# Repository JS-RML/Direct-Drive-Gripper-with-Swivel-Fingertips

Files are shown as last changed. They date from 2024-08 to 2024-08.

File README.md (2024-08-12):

# Direct-Drive Gripper with Swivel Fingertips (2024)

<!-- $\color{red}{\textsf{TOO MANY TYPOS! EACH TYPO IS A DEFECT!}}$ -->

We here introduce our latest direct-drive gripper. Compared to [the previous version](https://github.com/JS-RML/ddh_hardware) that we presented in [ICRA 2023](https://ieeexplore.ieee.org/document/10160263), the current one adopts swivel fingertips with passive compliance for enhanced adaptiveness. Follow the instructions below to create one. 

<p align = "center">

</p>

**Related repos**
- [**High-Speed Scooping (2024)**](https://github.com/JS-RML/Advanced-high-speed-scooping/tree/main)
- [**High-Speed Scooping (2022)**](https://github.com/JS-RML/high_speed_scooping)
- [**Direct-Drive Gripper (2022)**](https://github.com/JS-RML/ddh_hardware)

-----

# Table of Contents

- [Parts](#parts)
  - [Bill of Materials (BOM)](#bom)
    - [Off-the-Shelf Parts](#purchase)
    - [3D Printing](#3d-printing)
- [Motors](#motors)
  - [Motor Subassembly](#assemble-actuators)
  - [Wiring](#wiring)
    - [Power Supply](#power-supply)
    - [Encoder Connection](#encoder-connection)
    - [Motor Connection](#Motor-connection)
  - [Motor Calibration](#actuator-calibration)
    - [Calibrate ODrives](#calibrate-odrives)
    - [Calibrate Zero Position](#calibrate-zero-position)
- [Gripper](#Gripper)
  - [Finger Assembly ⨉2](#finger)
  - [Gripper Assembly](#gripper-assembly)
  - [Mounting](#mounting-ur10)
- [Customization](#customization)
  - [Mounting](#custom-mounting)
- [Getting Started](#getting-started)
  
-----

# Parts
Prepare for the following parts.

## Bill of materials (BOM)

### Off-the-shelf parts
- [T-motor gb54-2](https://store.tmotor.com/goods-445-GB54-2.html) X 4
- [Odrive s1](https://odriverobotics.com/shop/odrive-s1) X 4
- [AS5048A Encoder + solid magnet](https://ko.aliexpress.com/item/1005004239532357.html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) X 4
- [Bearing - outer-diameter = 100mm, inner-diameter = 6mm](https://kr.misumi-ec.com/vona2/detail/221000058378/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) X 12
- [Spring - spring constant = 2.0N/mm, length = 10mm, outer-diameter = 4φ](https://kr.misumi-ec.com/vona2/detail/110310295289/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) X 2
- [Wire terminal box](https://mini.freeship.co.kr/goods/content.asp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) X 1
- [Shielded cable](https://smartstore.naver.com/bantolmarket/products/10633794496) X 1
- [3-phase cable](https://smartstore.naver.com/shipdiy/products/7890381050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) X 3

### 3D Printing
- [Bearing_insert_holder](stl/bearing_insert_holder.stl) X 2
- [Bearing pin](stl/bearing_pin.stl) X 2
- [Distal link](stl/distal_link.stl) X 2
- [Distal tip cap left](stl/L_distal_tip_cap.stl) X 1
- [Distal tip spring version left](stl/L_distal_tip_spring_ver.stl) X 1
- [Distal tip cap right](stl/R_distal_tip_cap.stl) X 1
- [Distal tip spring version right](stl/R_distal_tip_spring_ver.stl) X 1
- [Finger tip](stl/finger_tip.stl) X 2
- [Motor shell](stl/motor_shell.stl) X 1
- [Motor plate](stl/motorplate.stl) X 4
- [Proximal link](stl/proximal_link.stl) X 2
- [Porximal link cap](stl/proximal_link_cap.stl) X 2
- [Proximal link pillar](stl/proximal_link_pillar.stl) X 2
- [Rotation limiter](stl/rotation_limiter.stl) X 2

# Motors
Parts related to motors can be put together as follows.
$\color{red}{\textsf{Missing links to the images below.}}$

## Motor Subassembly
We need four motor subassemblies. Each one can be assembled as follows.
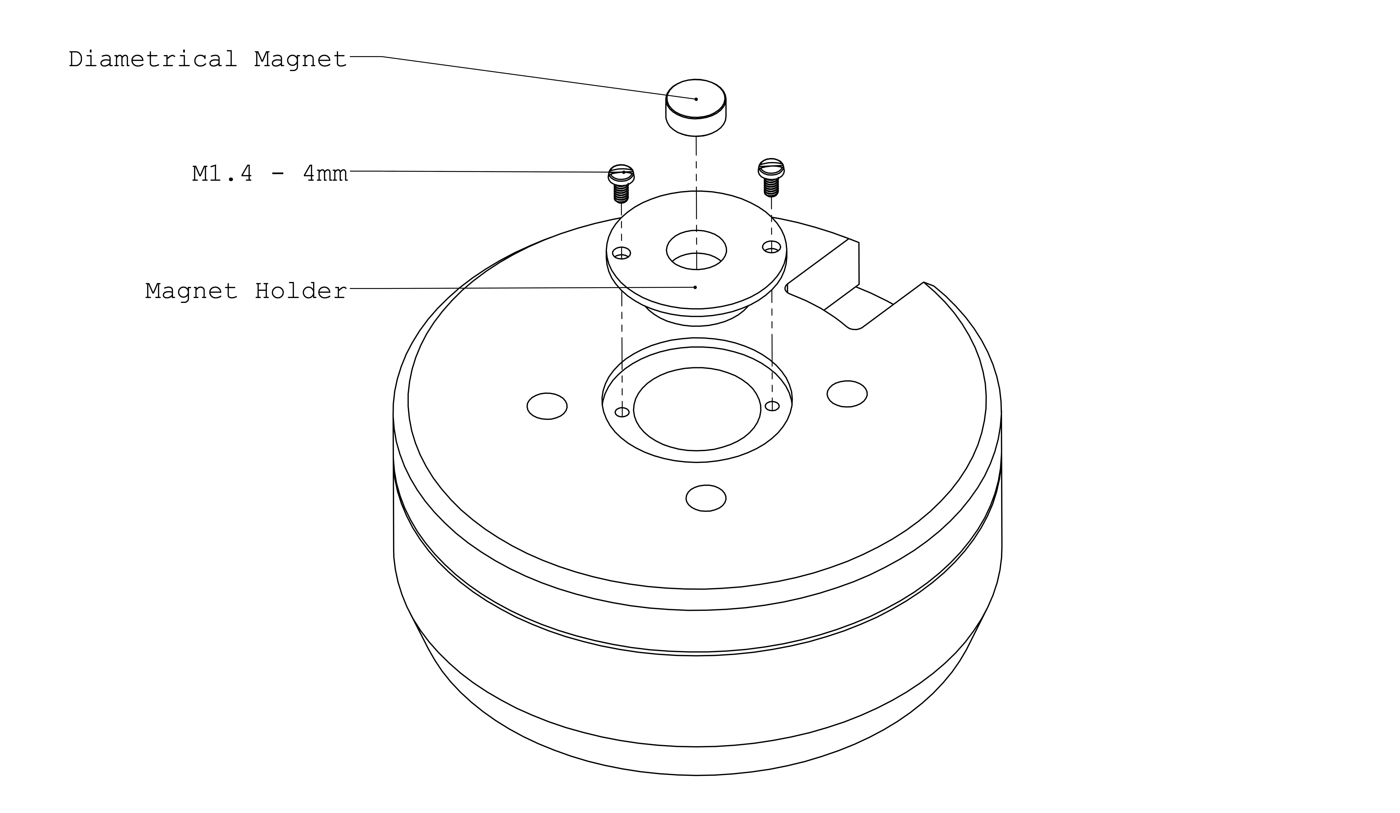
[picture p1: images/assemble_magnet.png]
motor_with_magnet

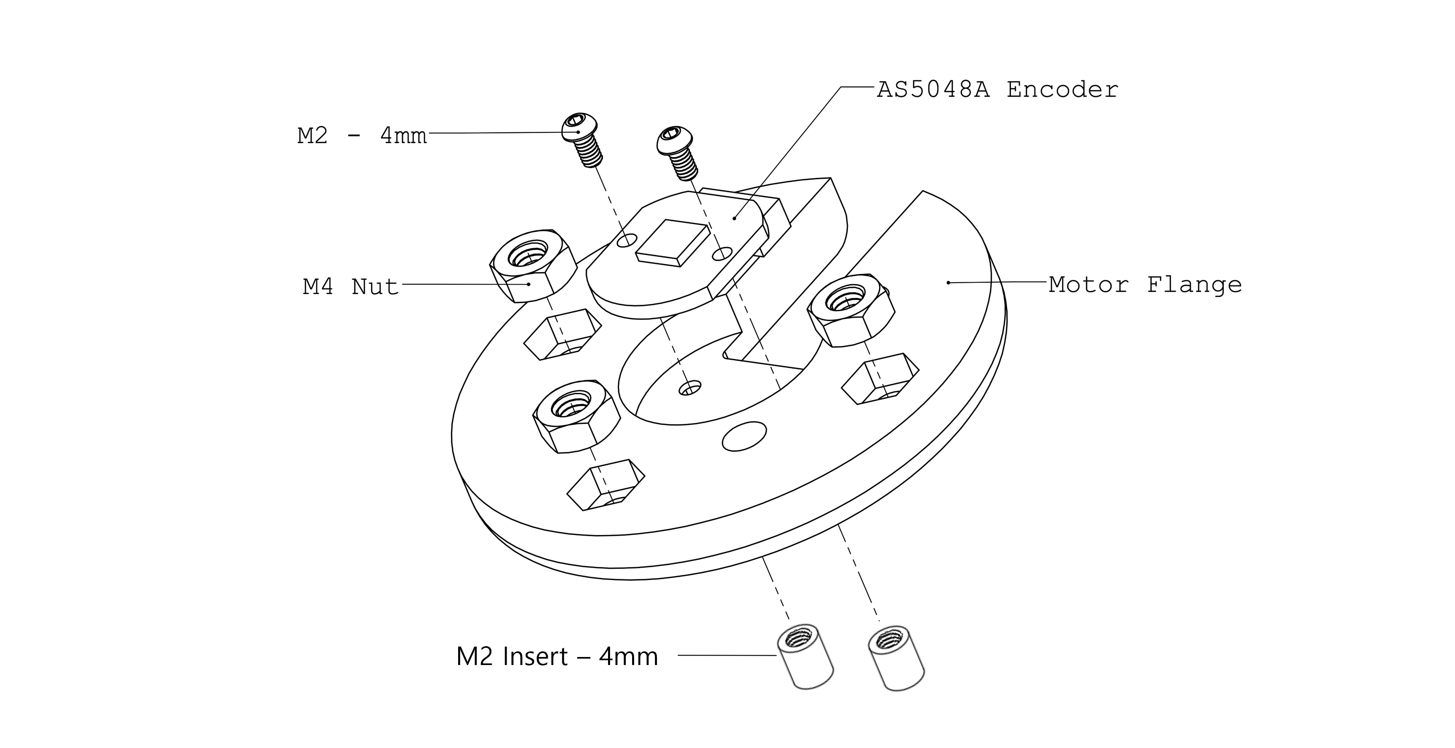
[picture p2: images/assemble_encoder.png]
motor-plate

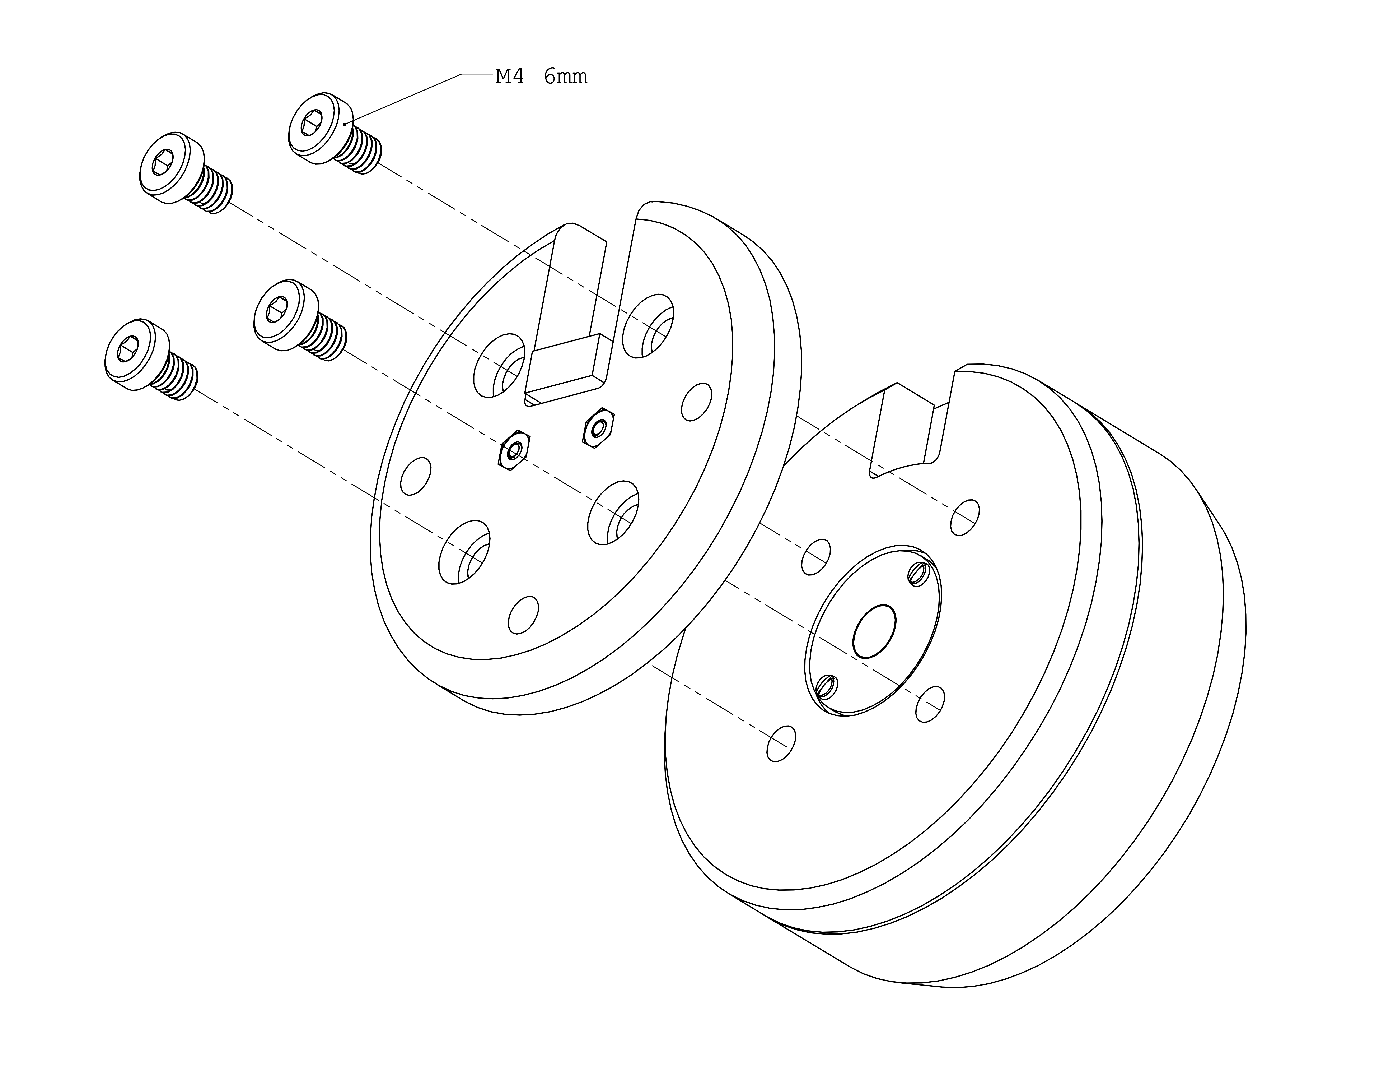
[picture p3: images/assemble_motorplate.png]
actuator-module


## Wiring
The components should be connected following the diagram below. The encoder connection(black) and power connection(green) will be further elaborated.
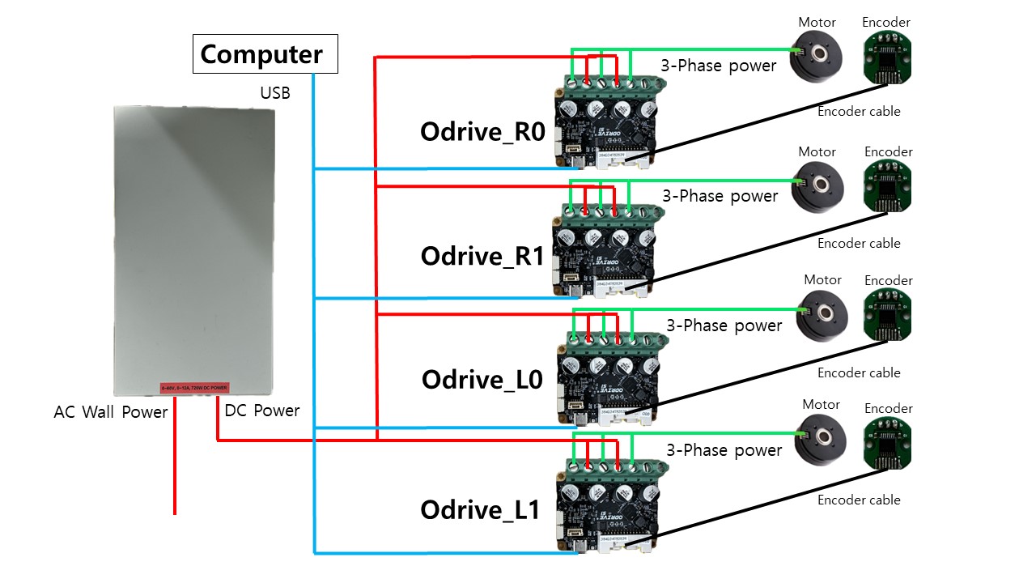
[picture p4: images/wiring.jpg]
wiring
 

### Power Supply
First connect the DC power supply to the wall plug. Then connect it to the four ODrive boards, positive to positive, negetaive to negative. There is no on/off button on the boards, plug in the wall plug to turn the system on, unplug to turn it off.
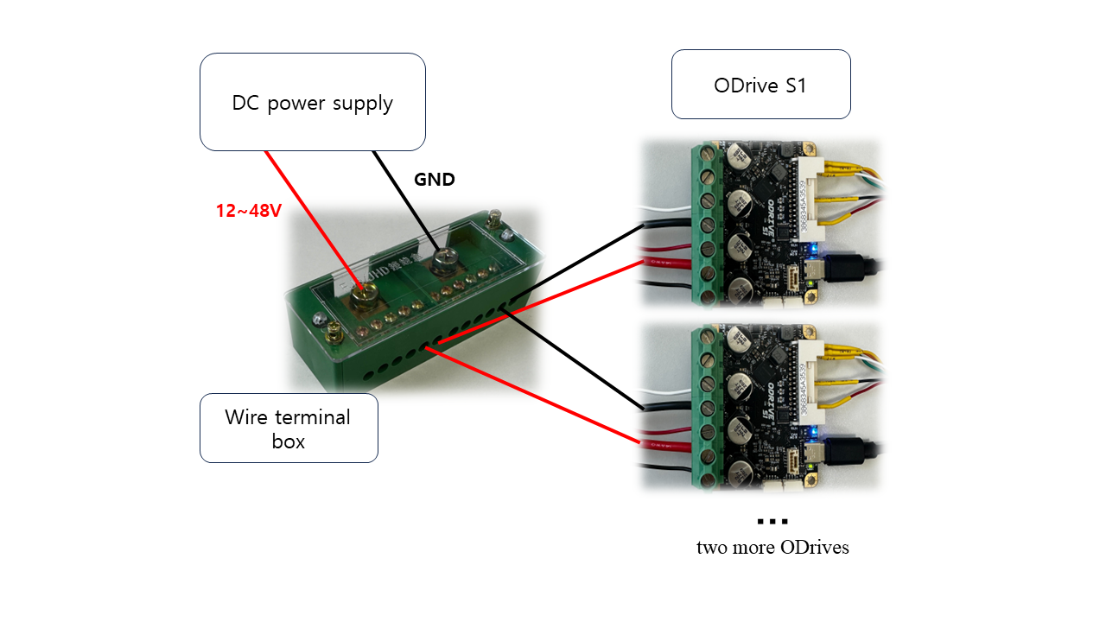
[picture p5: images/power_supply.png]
power_supply


### Encoder Connection
For the encoder connection, we fabricate a cable assembly as shown below in the schematic. It is recommended to verify the connectivity and resistance of each connection to make sure the cables are soldered properly. We also recommend to label each connector like the schematic.

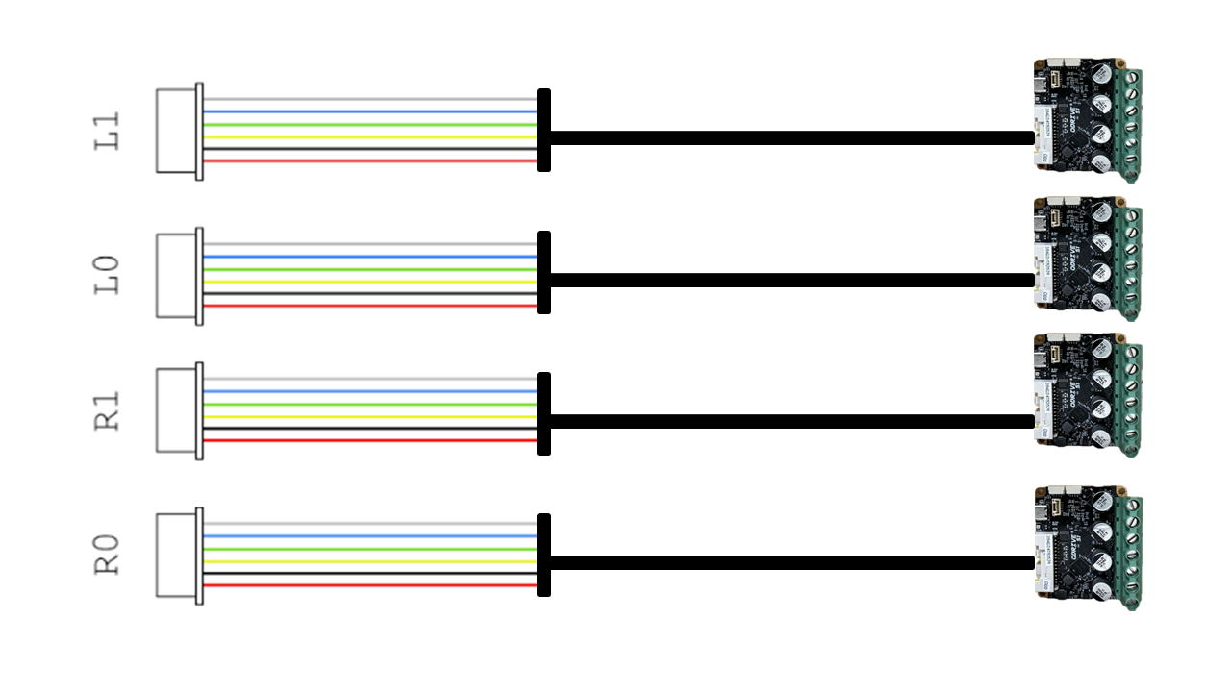
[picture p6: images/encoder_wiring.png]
encoder_wiring

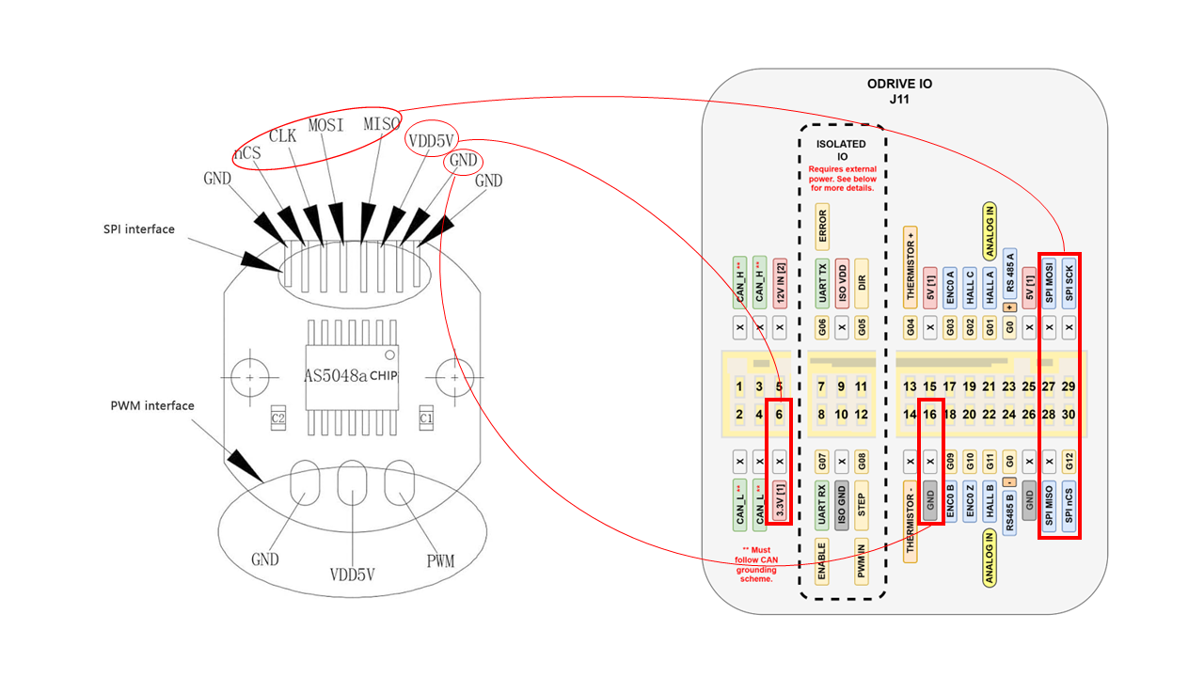
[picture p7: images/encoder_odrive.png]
encoder_odrive


After successful fabrication, connect the motor encoders and the ODrives.

### Motor Connection
Keep the 3-phase connection consistent as shown below.
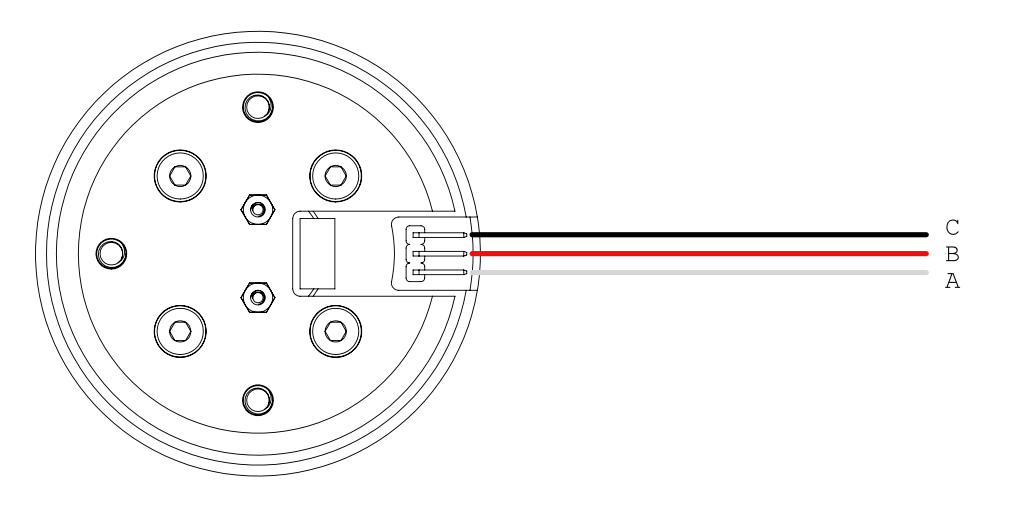
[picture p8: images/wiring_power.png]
wiring-power

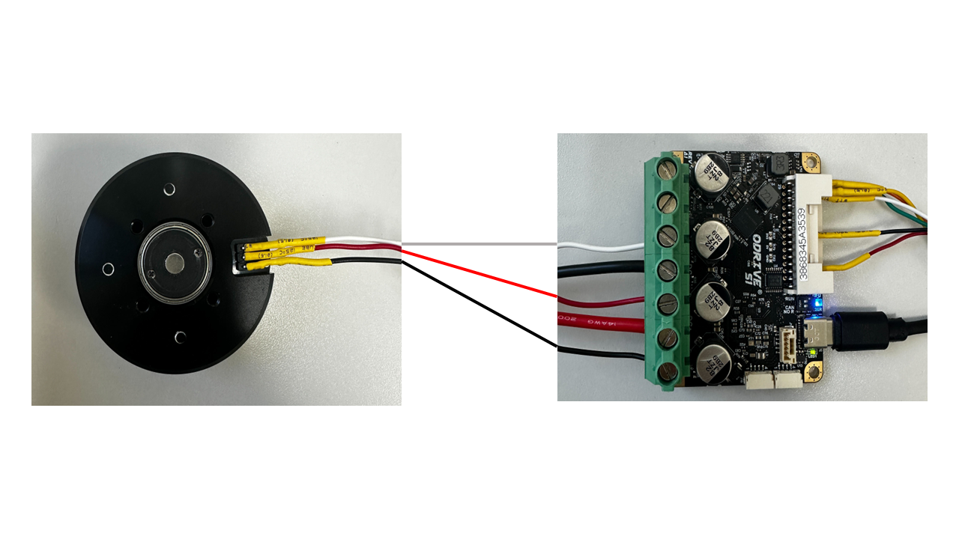
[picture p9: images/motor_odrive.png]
motor_odrive


### Odirve S1 Pin map.
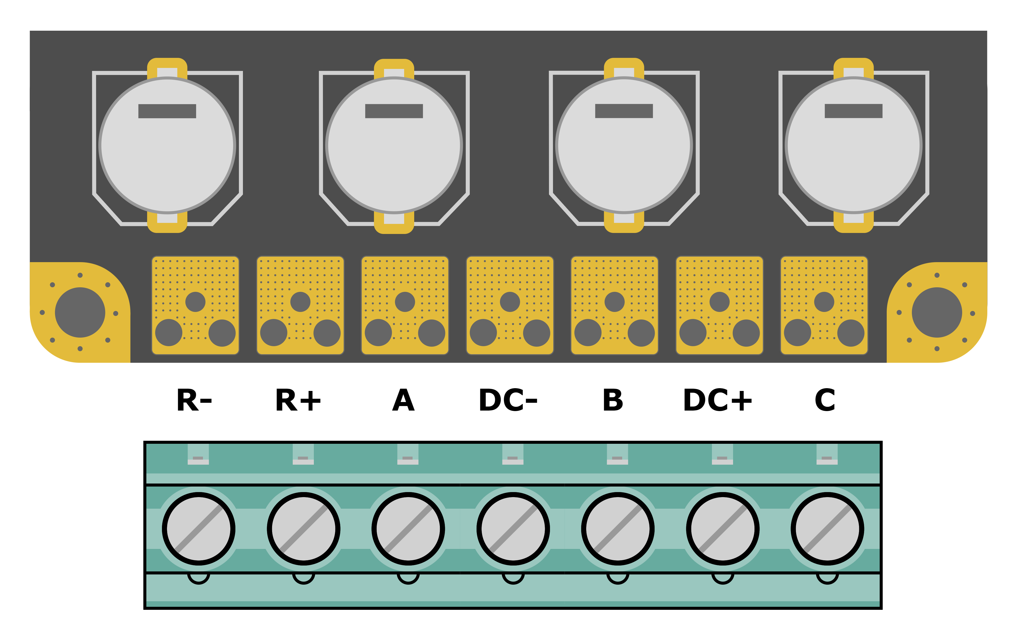
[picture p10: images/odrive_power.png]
odrive_power

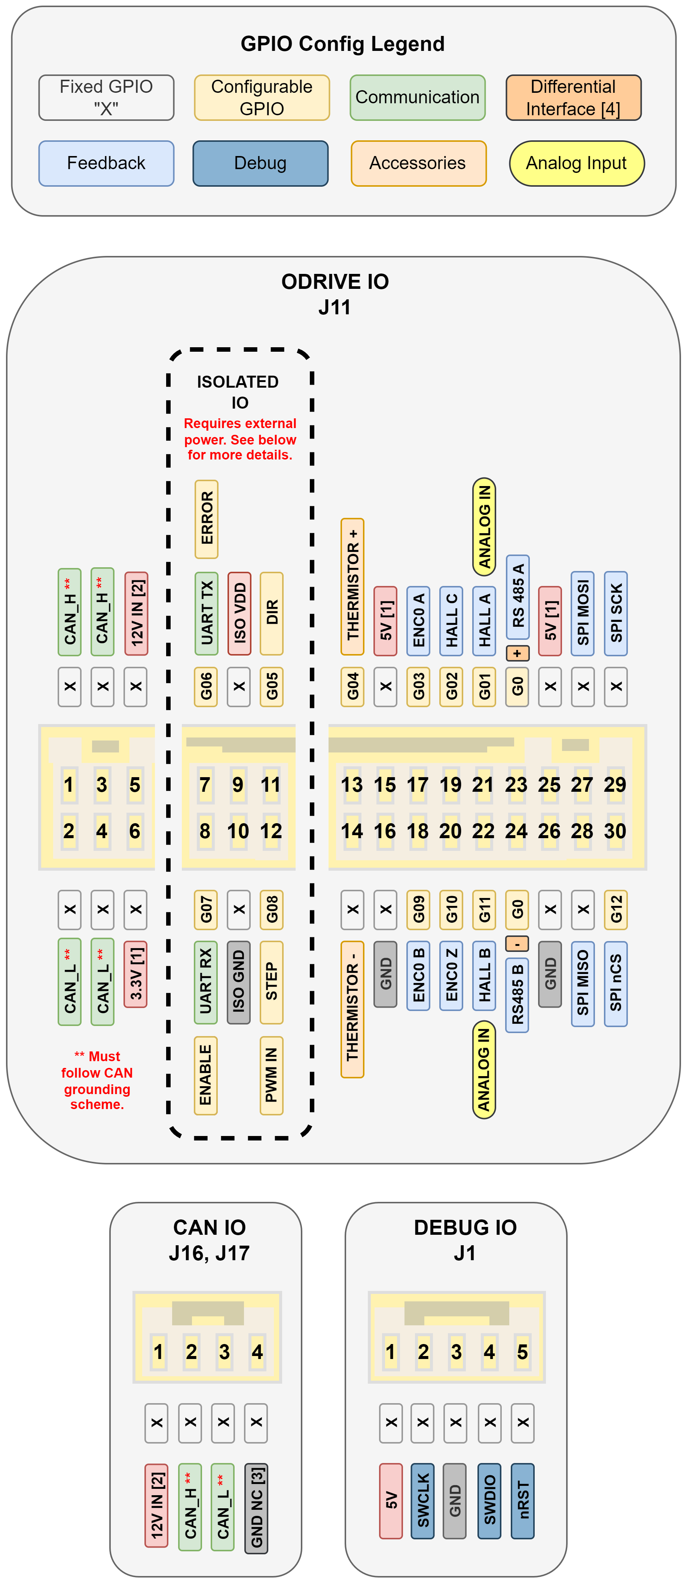
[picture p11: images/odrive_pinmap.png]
odrive_pinmap


# Motor Calibration

Each actuator module require calibration before use. This step __can not__ be done after the gripper is assembled, so do not postpone this step.

We explicitly define the `direction of the rotor` to be the direction the hexagonal logo on the rotor is pointing at, and the `zero position of the motor` to be when the direction of the motor is pointing at the opposite direction of the power port on the stator. 

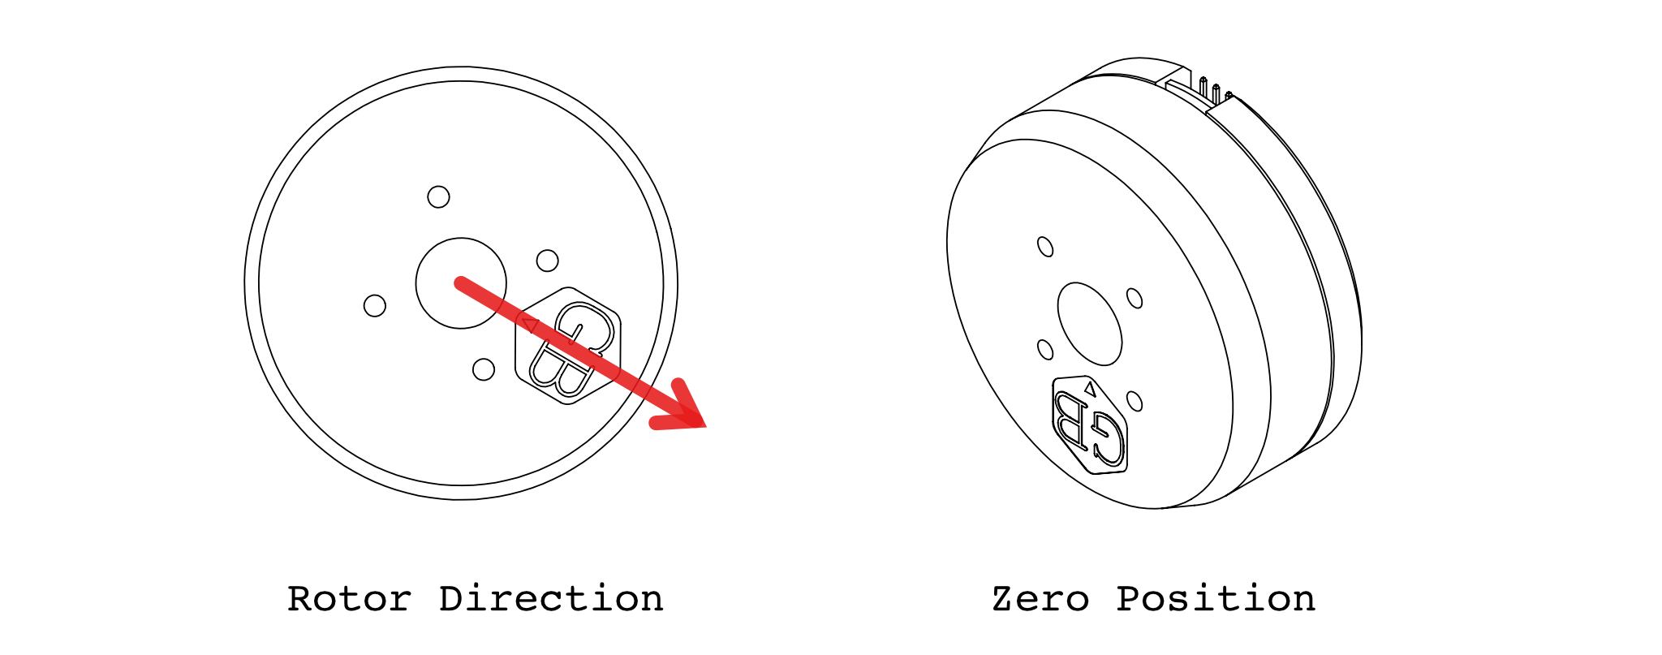
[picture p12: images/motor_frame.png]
motor-zero


## Calibrate ODrives
ODrive provides a GUI service for setting up the motordriver. ([Odrive GUI](https://gui.odriverobotics.com/inspector)) In the configuration tab in this GUI, You can set up the motordriver's configuration.
- Power source
  - DC bus overvoltage trip level: 26
  - DC bus undervoltage trip level: 22
  - DC max positive current: 'Leave it blank'
  - DC max negative current: -0.5
- Motor
  - Type: Gimbal
  - Phase resistance: 2.675
  - Pole pairs: 7
  - KV: 26
  - Current limit: 1
  - Motor calib current: 10
  - Motor calib voltage: 2
  - Lock-in spin current: 10
- Encoder
  - Type: SPI(AMS protocol)
  - nCS pin: GPIO 12
- Control mode
  - control mode: Position Control
  - Soft velocity limit: 10
  - Hard velocity limit: 13.75
  - Torque limit: 0.192
- Interface
  - UART(115200)

## Calibrate Zero Position

Here we calibrate the zero position of the motor. Mount the actuator on the calibration stand and install the calibration arm onto the actuator according to the diagram

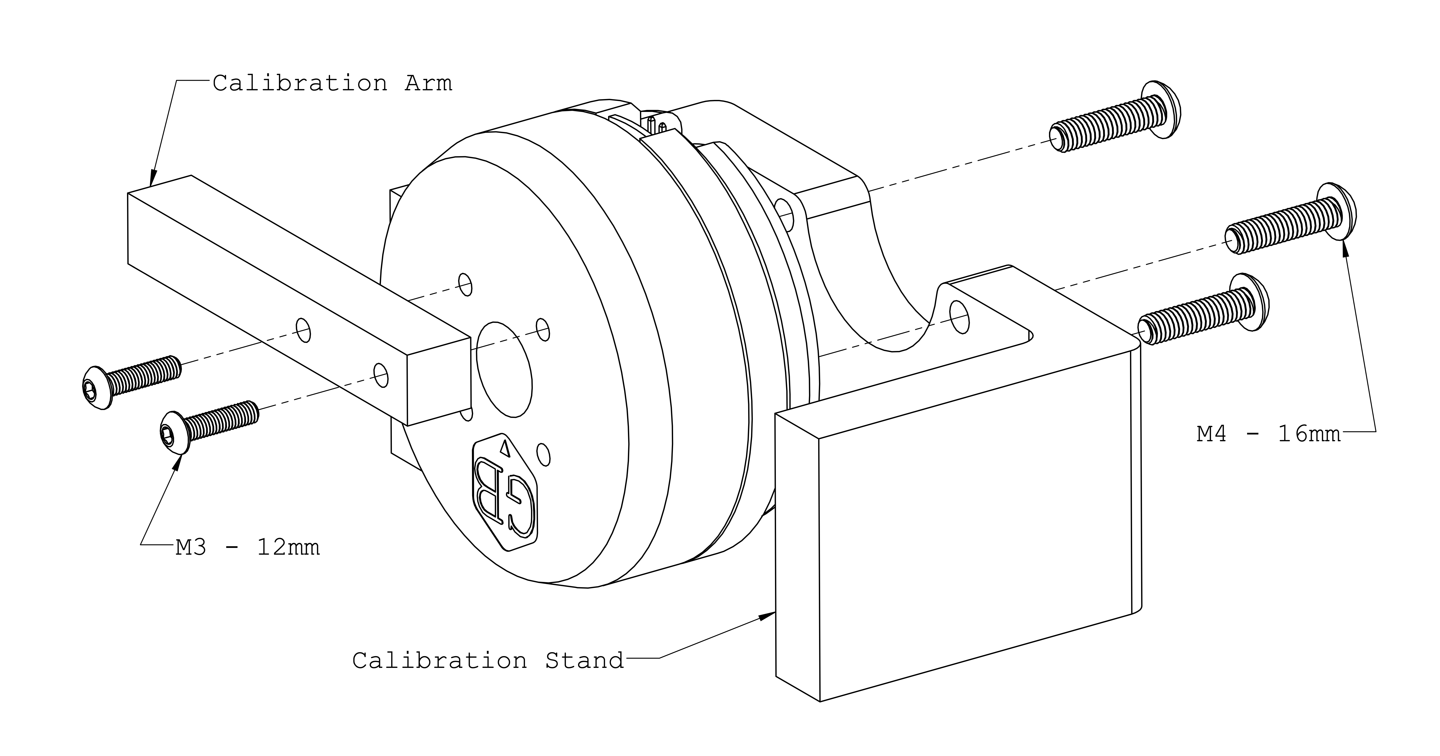
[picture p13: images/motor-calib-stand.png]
calibration-stand


Put the motor into zero position as show in the diagram below. Press down the calibration arm to make sure the stand and arm touch tightly. 

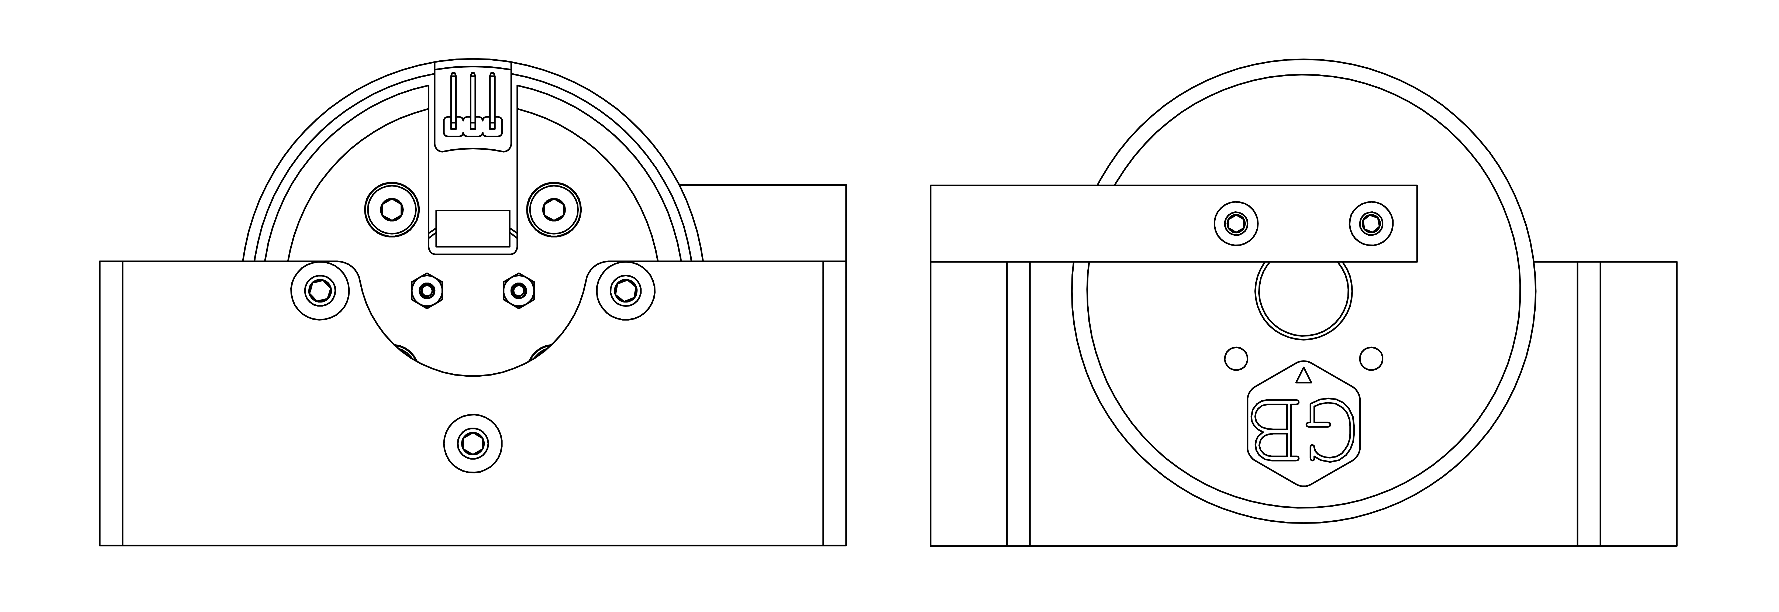
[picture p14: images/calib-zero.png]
zero-stop


Check the 'pos_estimate' value of each odrive(ODrive0, ODrive1, ODrive2, ODrive3...) in the 'inspector' tab of the [Odrive GUI](https://gui.odriverobotics.com/inspector) and memorize this value. Later, you will use this value to set motor offset when you create the 'Actuator' object.

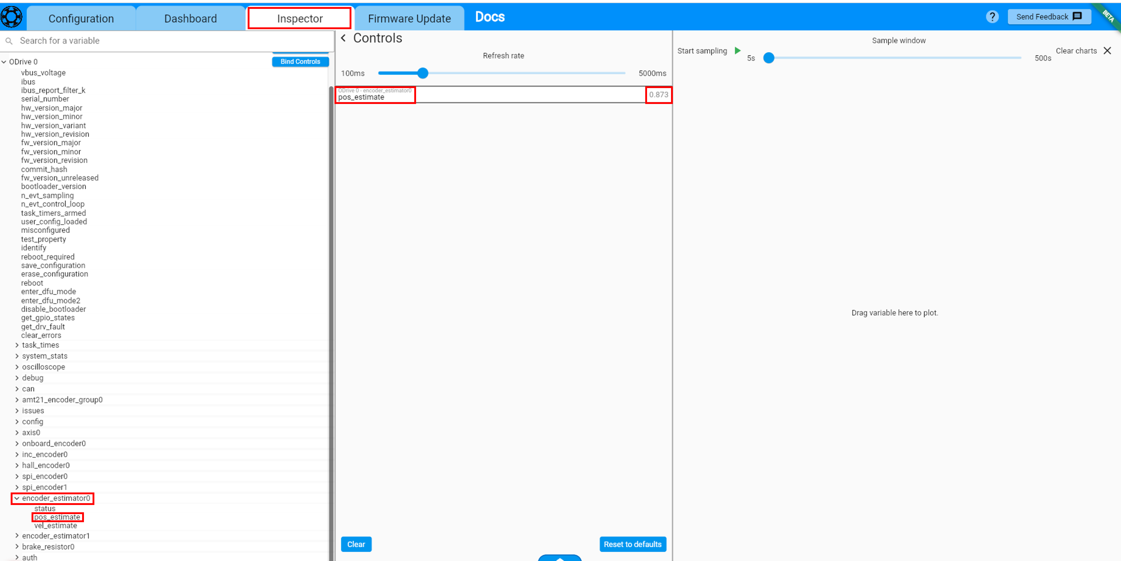
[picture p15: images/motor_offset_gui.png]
motor_offset_gui


# Gripper

## Finger Assembly ⨉ 2

You sholud insert the bearings in the red circle.

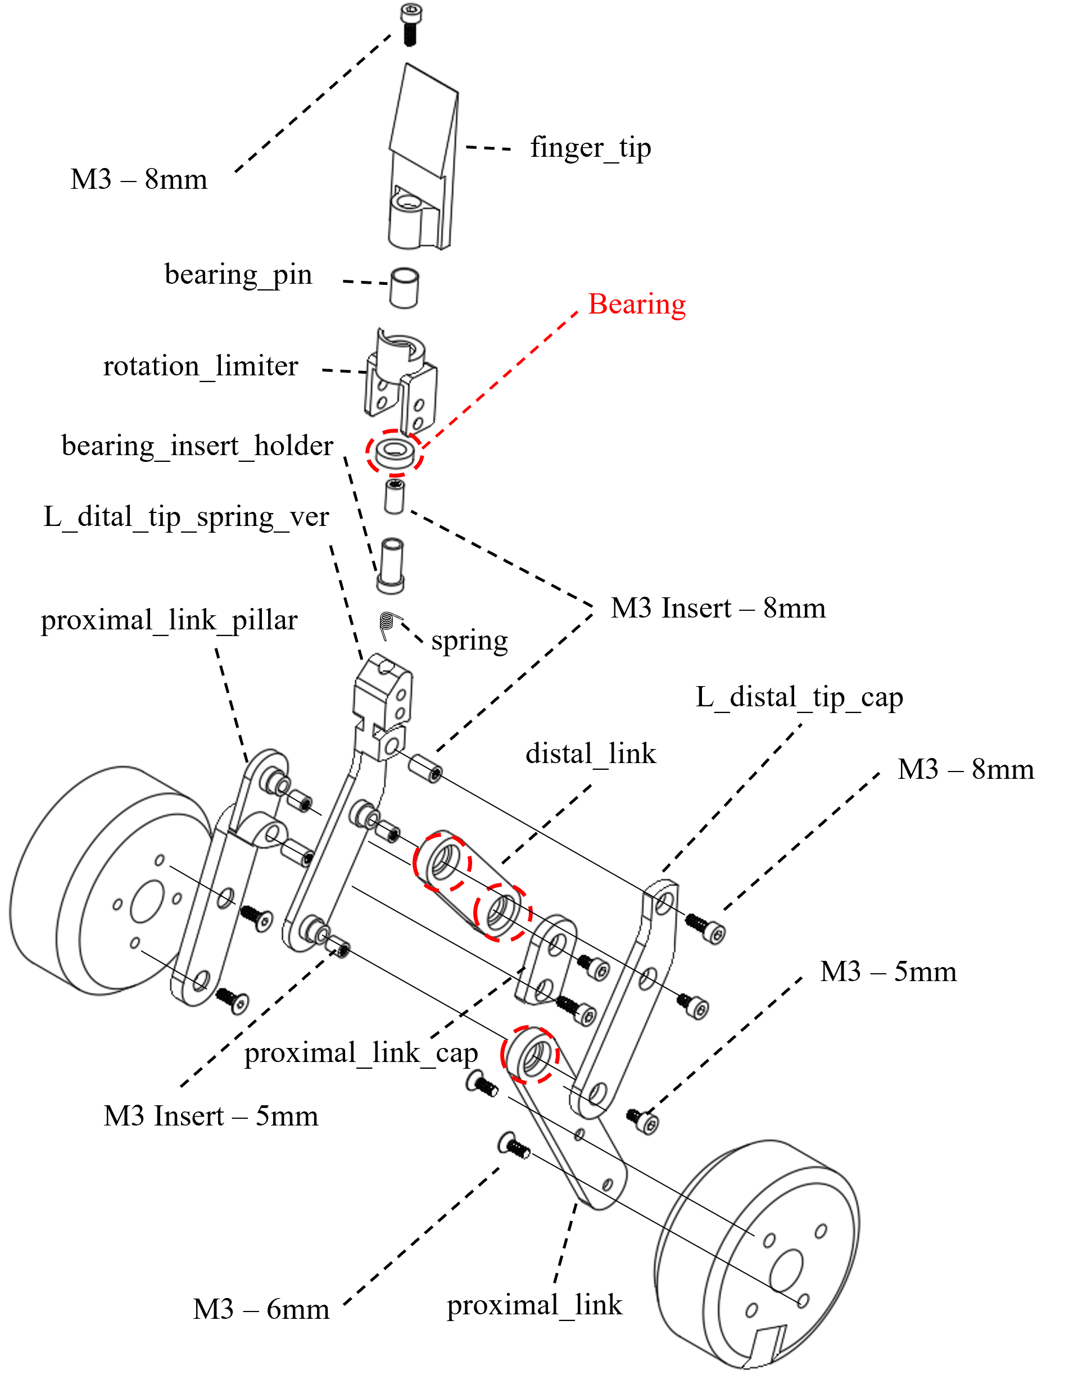
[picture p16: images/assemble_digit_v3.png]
finger


## Gripper Assembly

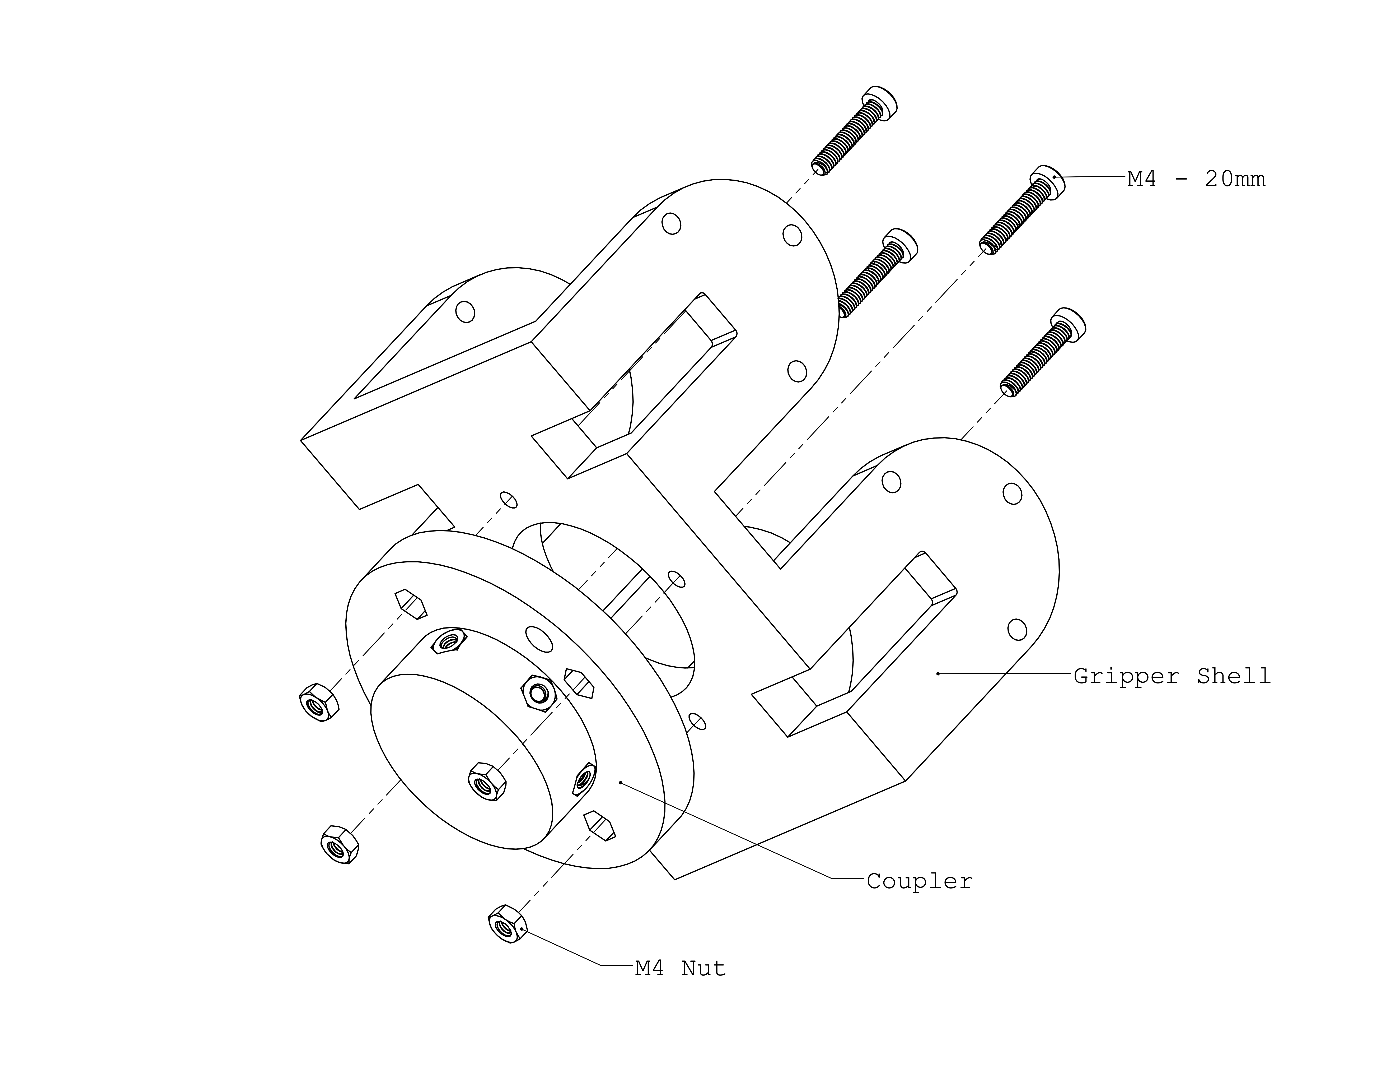
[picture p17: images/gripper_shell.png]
gripper_shell


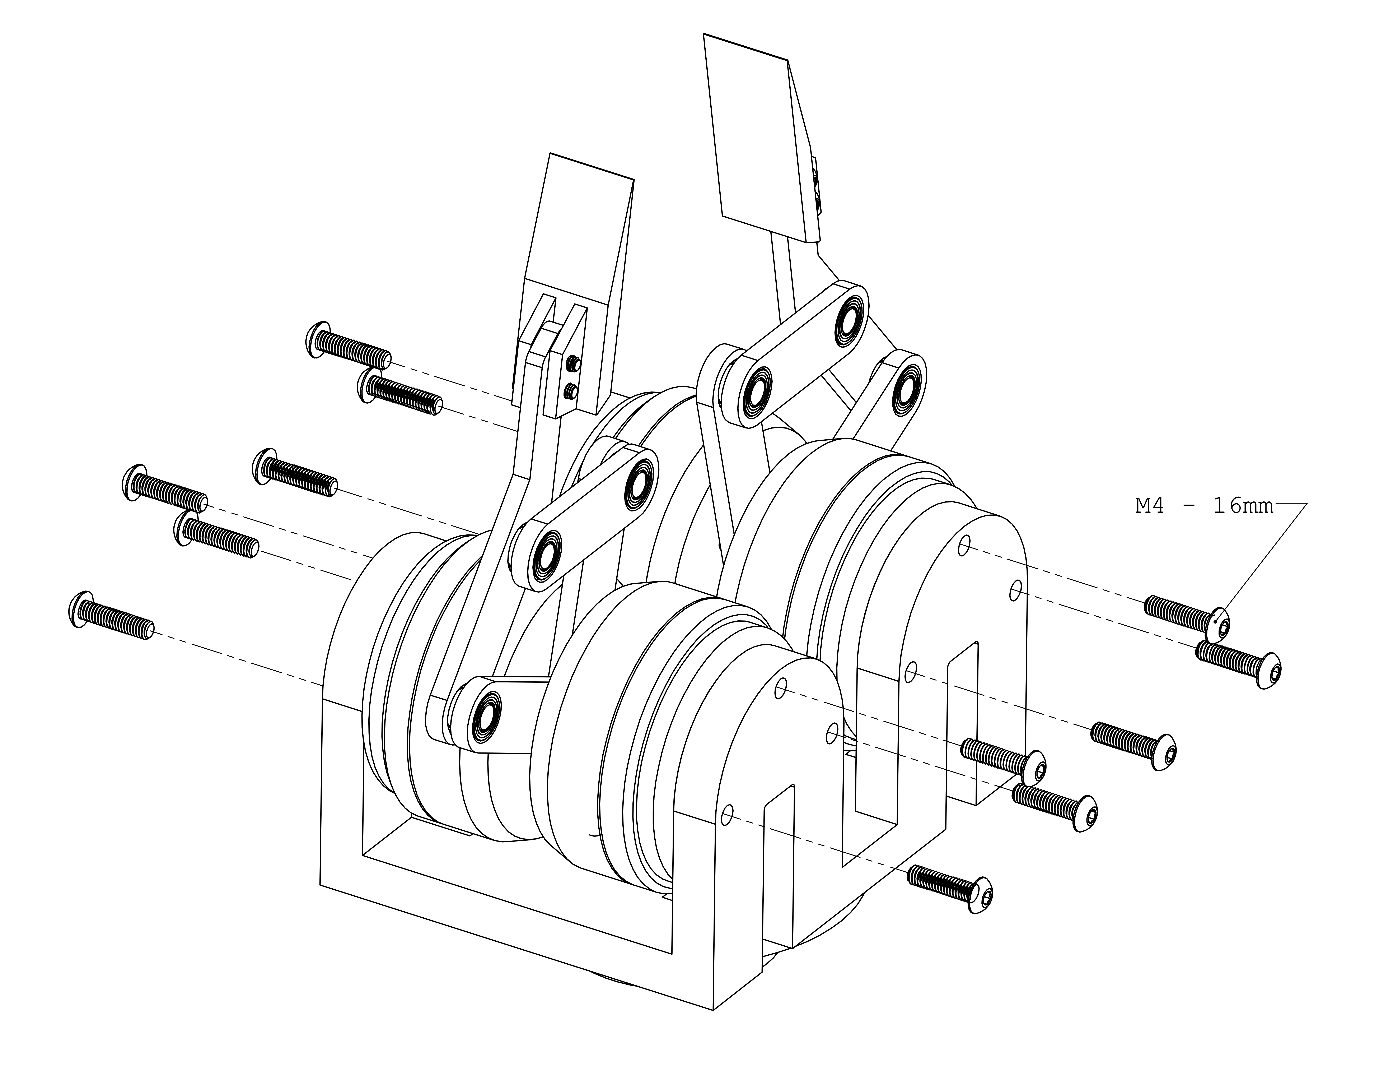
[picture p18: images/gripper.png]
gripper


## Mounting

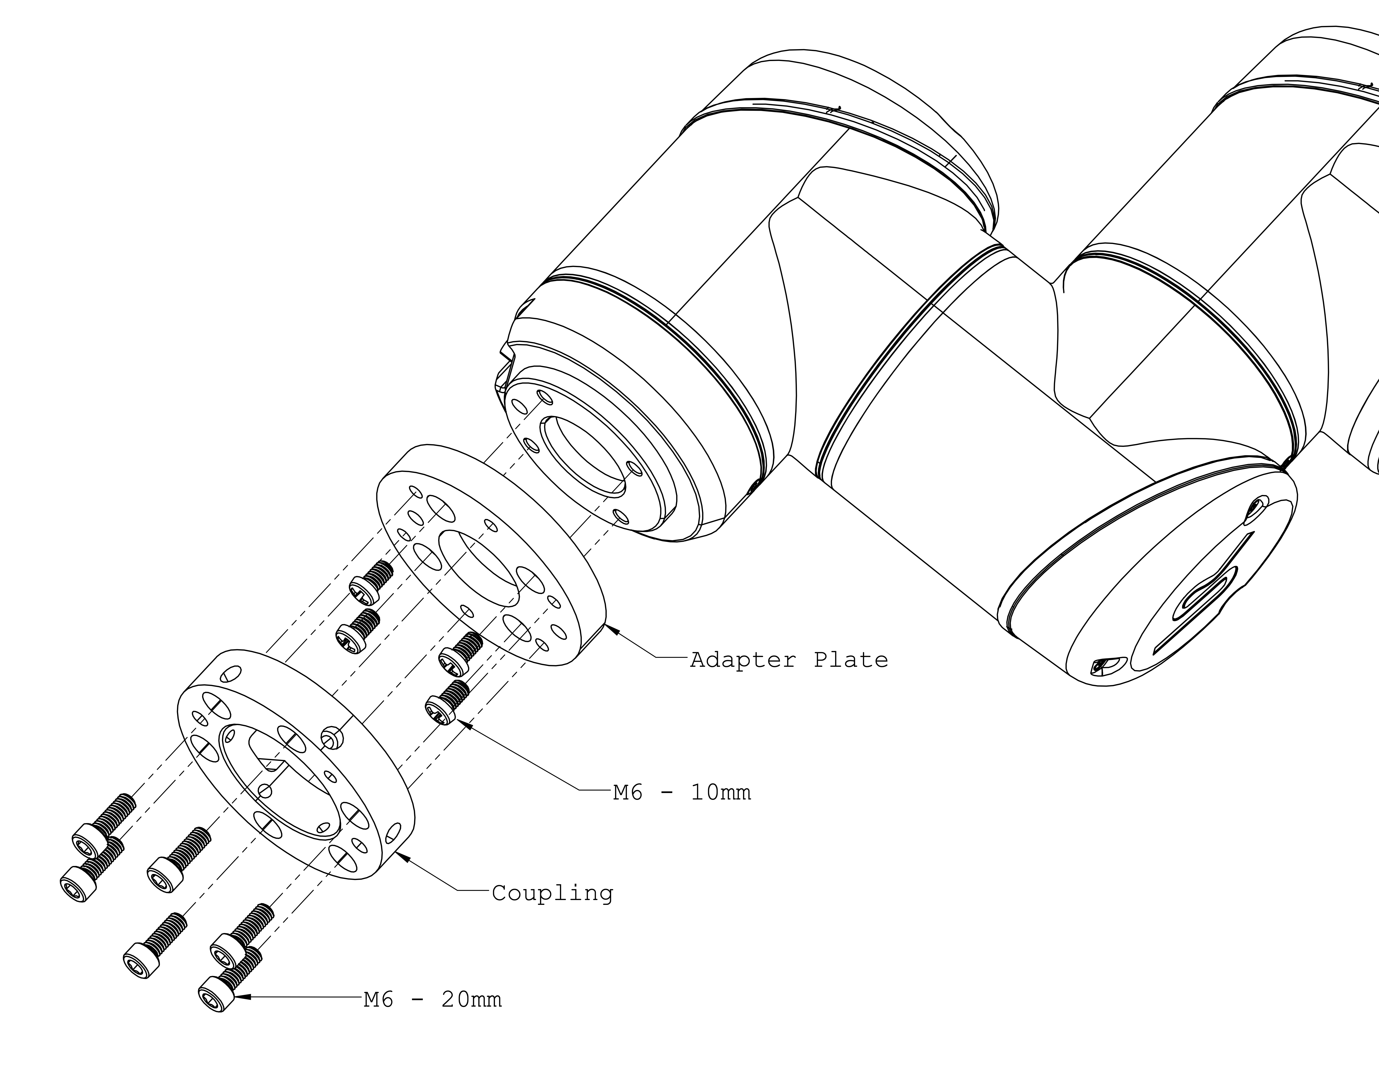
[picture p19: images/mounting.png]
mounting


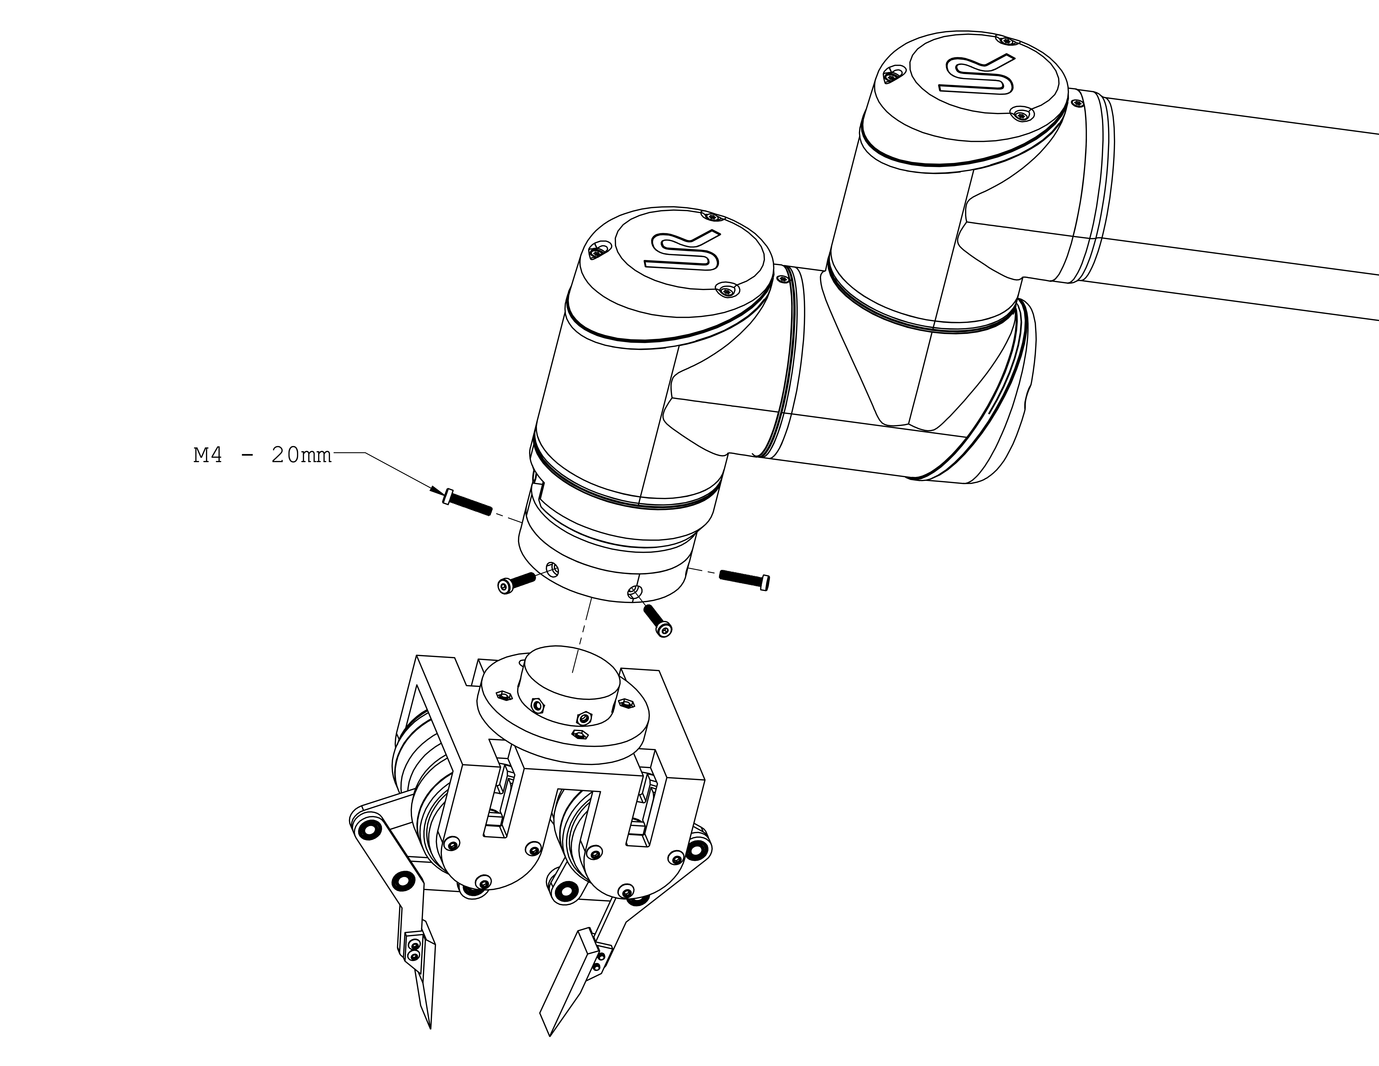
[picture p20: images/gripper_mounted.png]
gripper_mounted


# Customization

## Mounting

If the default mounting does not work for you, it's very easy to make a custom mount. The gripper has a __60 mm PCD with 4 ⨉ M4__ mounting interface, as shown in the drawing below.
<br/><br/>The gripper is designed to be compatible with Rainbow robotics RB5. For other robot systems, it would be better to customize the adapter plate and coupling.
$\color{red}{\textsf{Move this statement to those parts that need to be redesigned. Or does this apply to all the parts?}}$
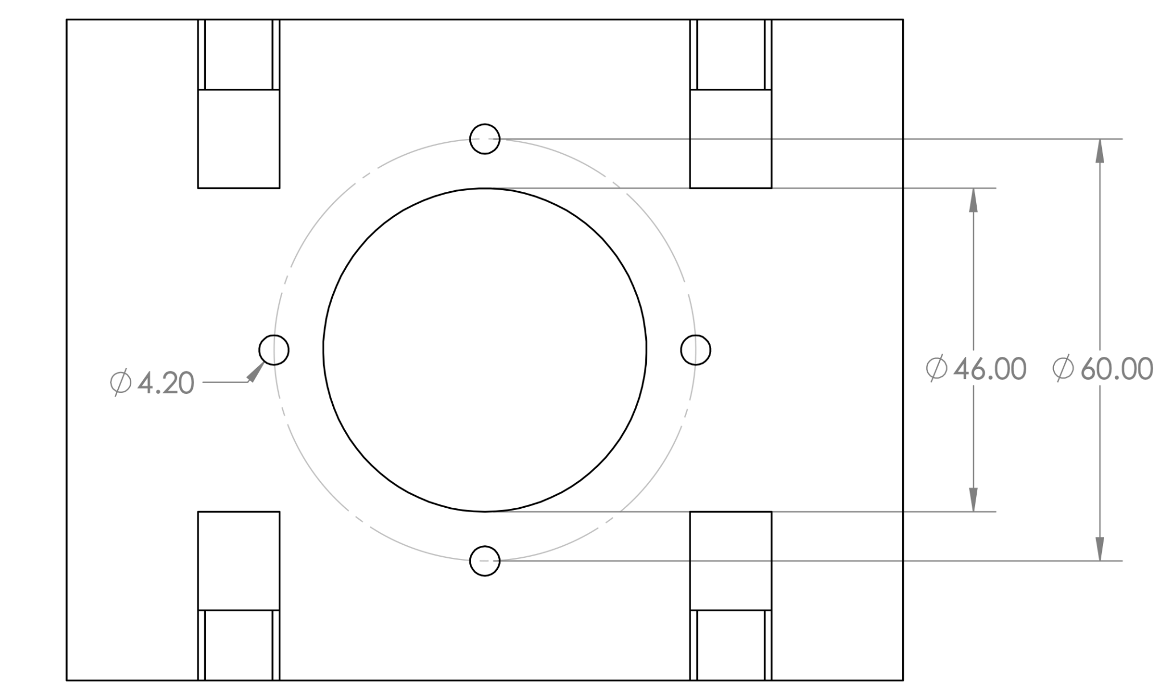
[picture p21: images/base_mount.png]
base_mount


-----
# Software
Our software is implemented with **python3** and tested on **Ubuntu**. You can also refer to this website https://docs.odriverobotics.com/v/latest/guides/getting-started.html.

### Versions ###
- ubuntu : 20.04
- Python : 3.10.11
- Odrive control untility : 0.6.7

### Getting started ###
1. First, you should install accompanying PC program for the ODrive, 'odrivetool'.
```bash
pip install --upgrade odrive
```
2. Set up USB device permissions.
```bash
sudo bash -c "curl https://cdn.odriverobotics.com/files/odrive-udev-rules.rules > /etc/udev/rules.d/91-odrive.rules && udevadm control --reload-rules && udevadm trigger"
```
3. To launch the main interactive ODrive tool, type 'odrivetool'. And then, type 'odrv0.vbus_voltage' to inspect the boards main supply voltage.
```bash
odrivetool
```
&nbsp;&nbsp;&nbsp;&nbsp;If the program is installed and the odrive is connected successfully, then you can see the messages.
```bash
ODrive control utility v0.6.7
Please connect your ODrive
You can also type help() or quit().

Connected to ODrive S1 384D34783539 (firmware v0.6.7) as odrv0
In  [1]: odrv0.vbus_voltage
Out [1]: 23.931137084960938
```
-----

# Contributors
- Hyeonje Cha, guswp3611@gmail.com
- Seunghwa Oh, seunghwa9118@pusan.ac.kr

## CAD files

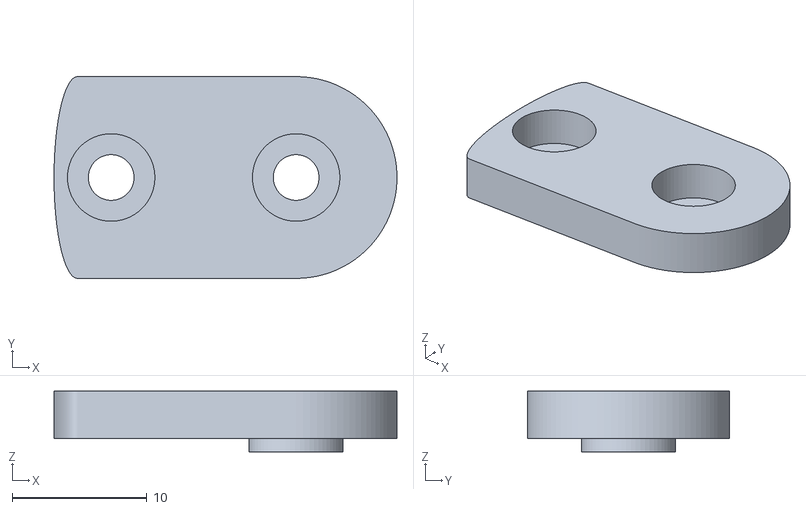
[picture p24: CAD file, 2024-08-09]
stl/proximal_link_cap.stl
25.5 x 15.0 x 4.50

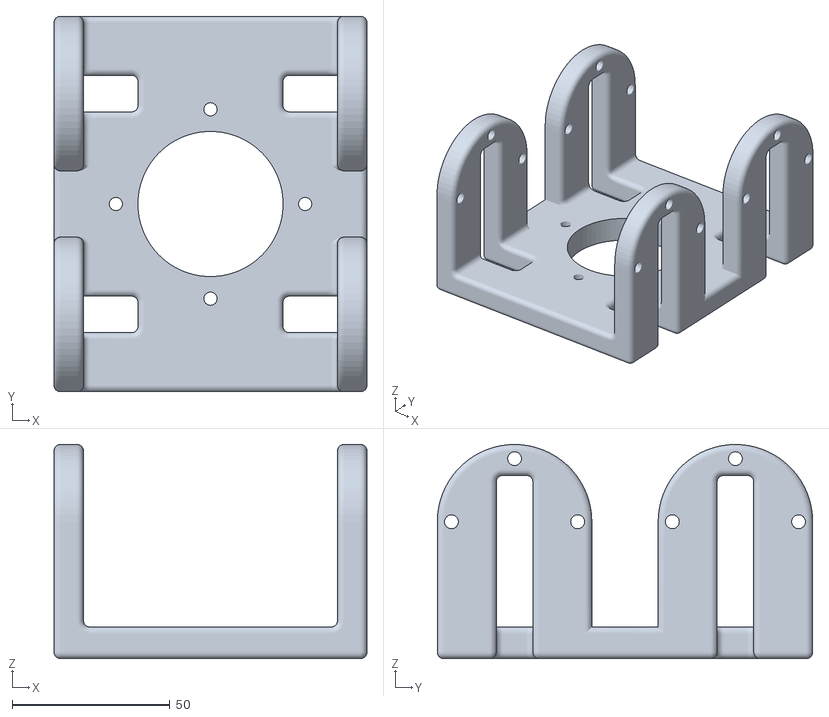
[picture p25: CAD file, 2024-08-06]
stl/motor_shell.stl
99.2 x 119.0 x 67.8

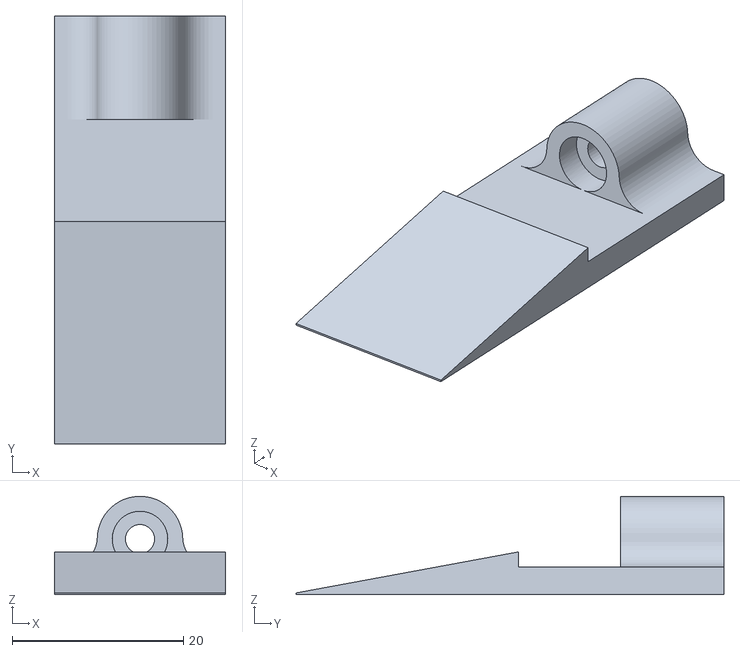
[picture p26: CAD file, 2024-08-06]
stl/finger_tip.stl
20.0 x 50.0 x 11.5

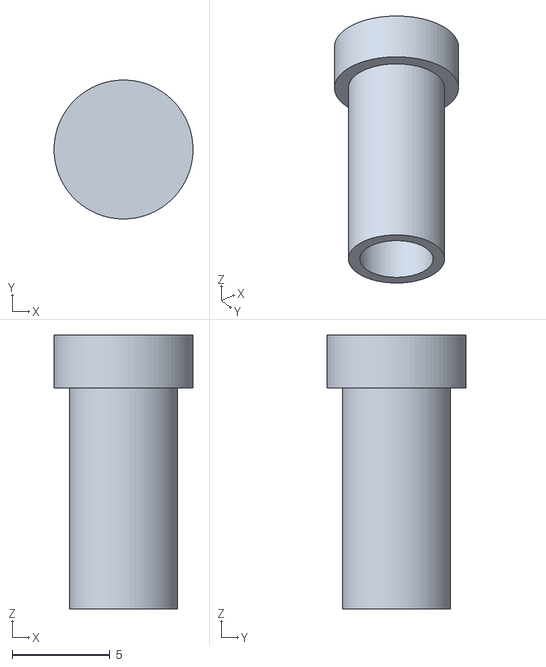
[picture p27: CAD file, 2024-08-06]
stl/bearing_insert_holder.stl
7.10 x 7.10 x 14.0

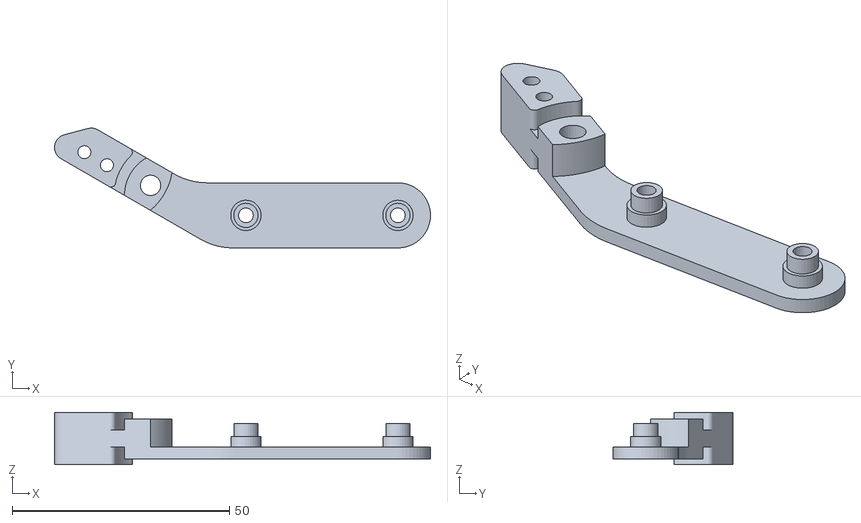
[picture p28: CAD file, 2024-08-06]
stl/R_distal_tip_spring_ver.stl
86.6 x 27.6 x 12.0

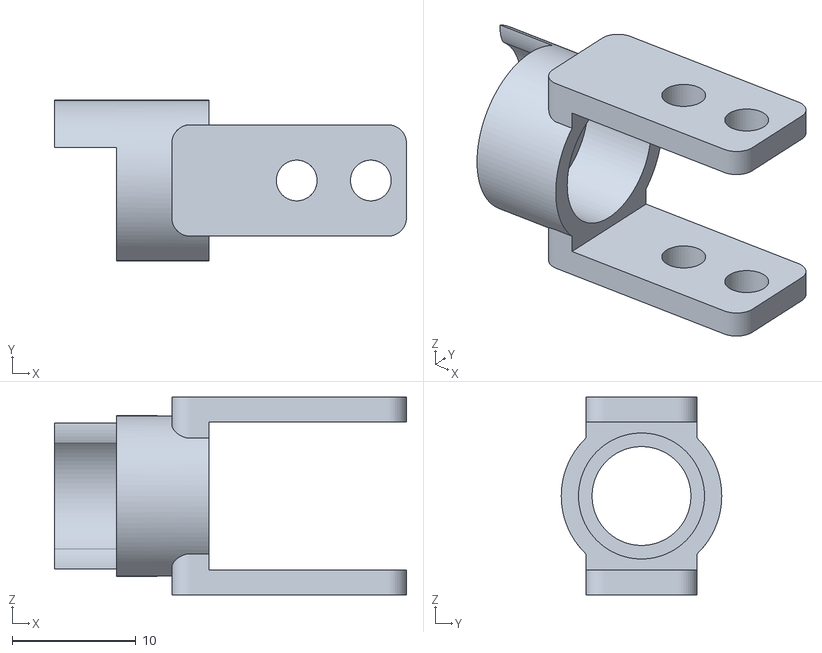
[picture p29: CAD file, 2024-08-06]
stl/rotation_limiter.stl
28.5 x 13.0 x 16.0

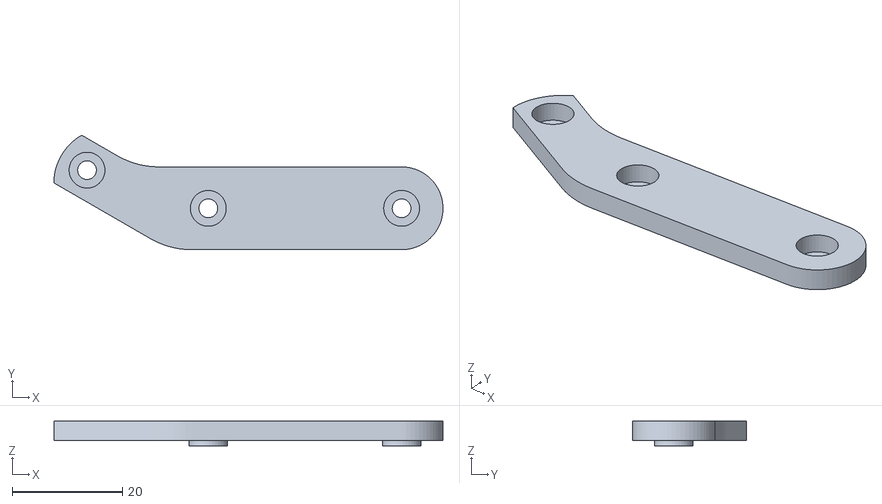
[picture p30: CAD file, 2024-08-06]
stl/R_distal_tip_cap.stl
70.4 x 20.7 x 4.50

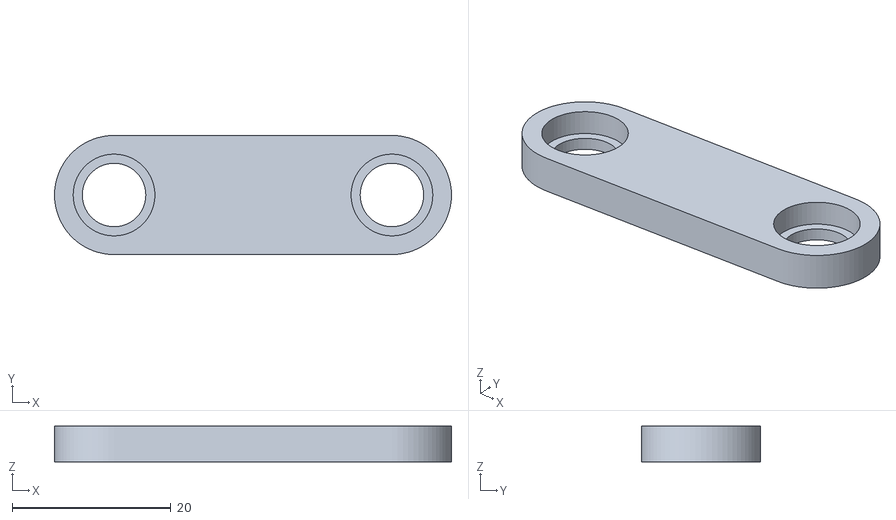
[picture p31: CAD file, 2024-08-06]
stl/distal_link.stl
50.0 x 15.0 x 4.50

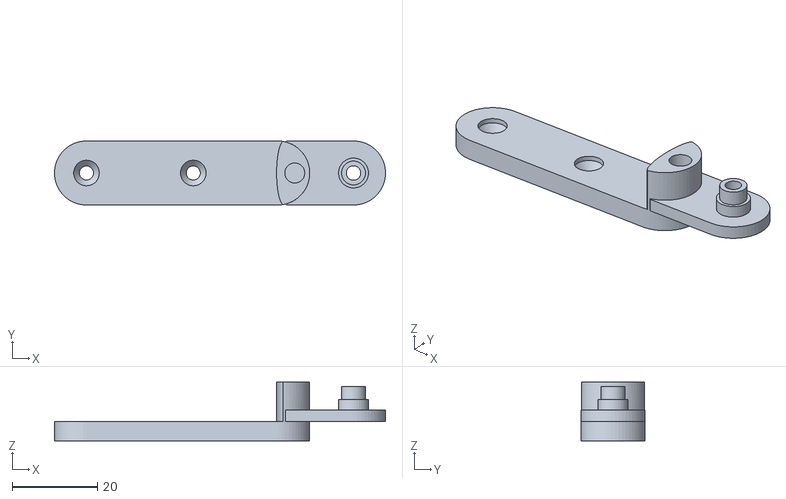
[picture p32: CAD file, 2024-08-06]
stl/proximal_link_pillar.stl
77.5 x 15.0 x 13.7

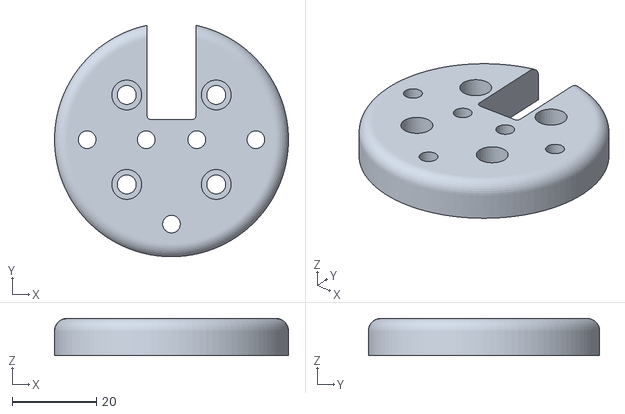
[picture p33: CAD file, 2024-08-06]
stl/motorplate.stl
55.5 x 54.9 x 8.85

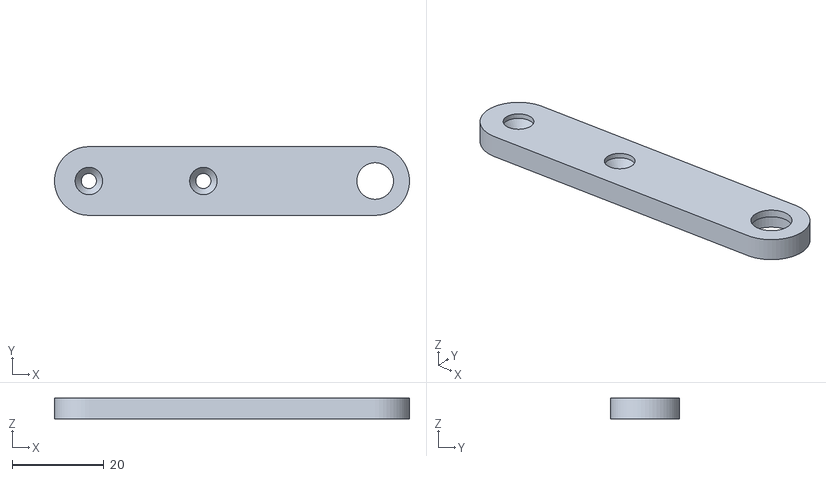
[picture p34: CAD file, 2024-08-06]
stl/proximal_link.stl
77.5 x 15.0 x 4.50

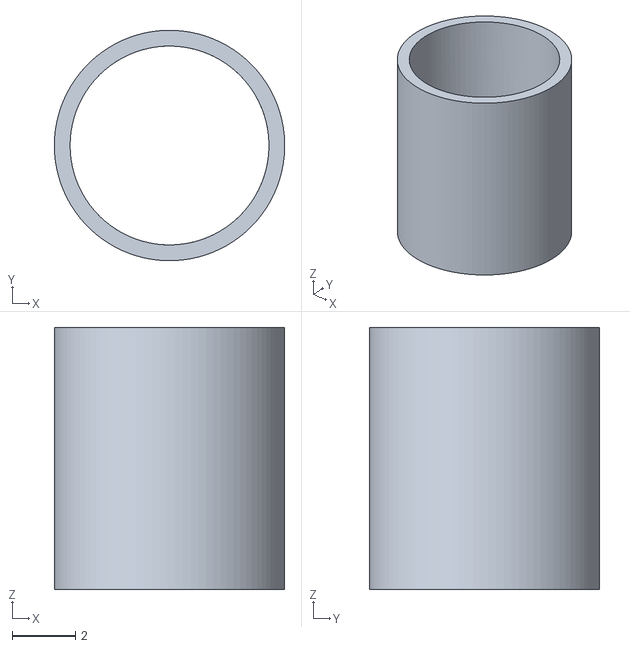
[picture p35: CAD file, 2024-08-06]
stl/bearing_pin.stl
7.30 x 7.30 x 8.30

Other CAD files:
stl/L_distal_tip_cap.stl
stl/L_distal_tip_spring_ver.stl

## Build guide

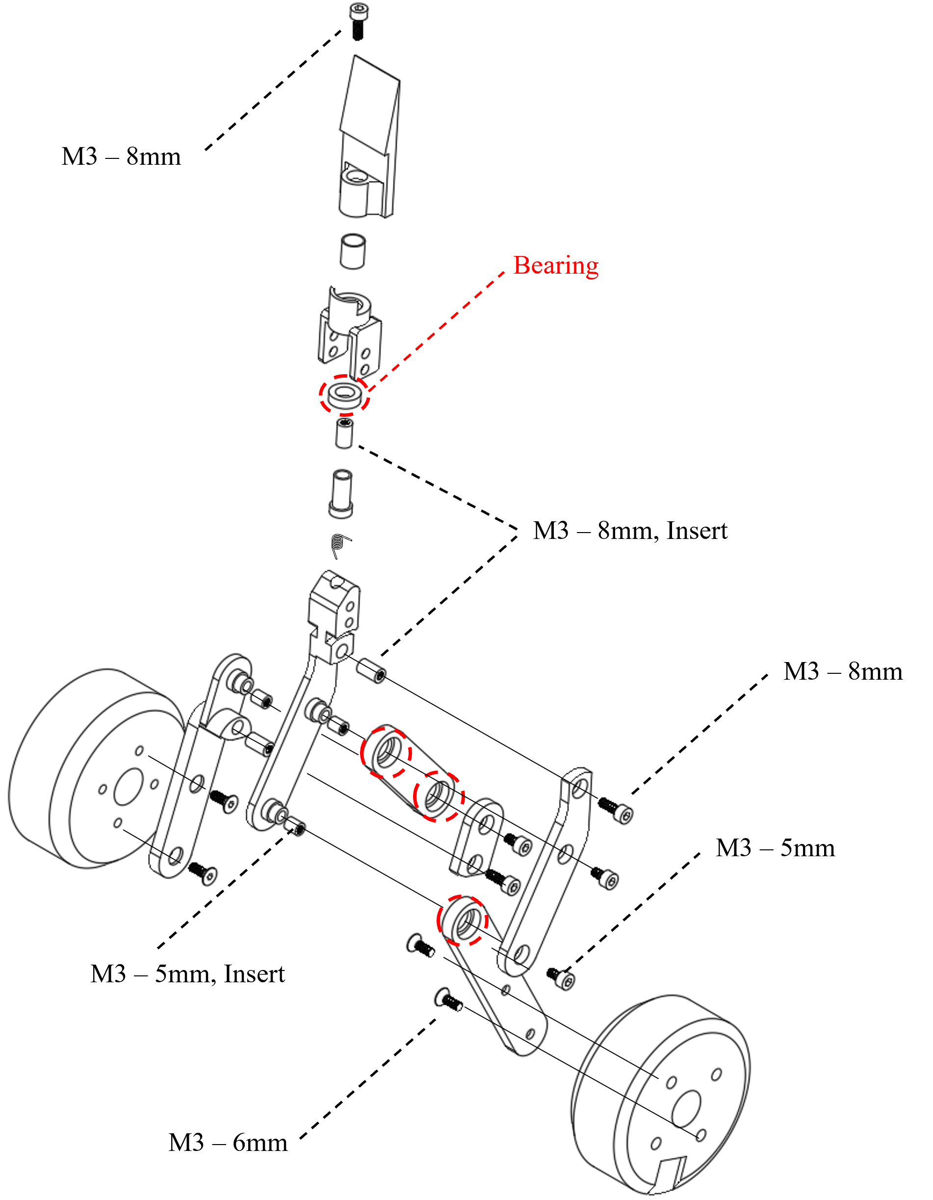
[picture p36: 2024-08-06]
images/assemble_digit.png
